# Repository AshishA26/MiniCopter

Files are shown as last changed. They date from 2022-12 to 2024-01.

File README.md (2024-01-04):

# MiniCopter
A mini quadcopter that is lightweight (~100g) and designed for agility. It is made using an Arduino Nano, an MPU6050 for orientation sensing, an NRF24L01 for wireless communication, MOSFETs that act as motor drivers, and 8520 motors. The quadcopter is controlled using a custom transmitter that has 2 joysticks and an NRF24L01, and uses PID motor control for stabilizing roll and pitch of the quadcopter. In addition, I created a custom PCB to house all these components and allow for better wiring, testing, and weight reduction.

Programmed in `Arduino IDE`, models created in `Autodesk Inventor`, schematics and PCB created in `KiCad`.

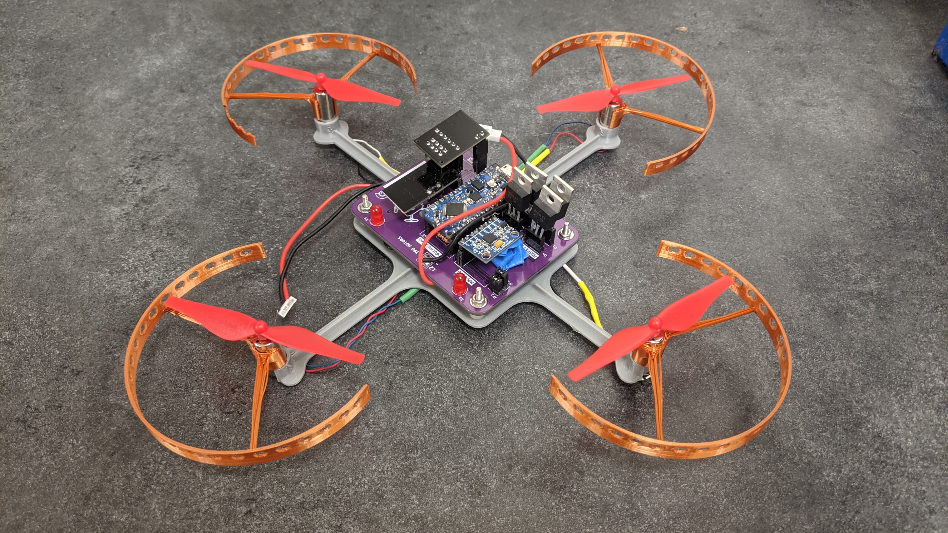
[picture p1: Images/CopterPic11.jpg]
CopterPic11

CopterGif1

Demo showing the PID motor control of the quadcopter that allows for the quadcopter to stabilize and balance ([full video](https://www.youtube.com/watch?v=k4_8MwJ_Zw4)):
CopterGif2

## PCB Design
My original design used a perfboard, but I eventually designed a 2-layer PCB that would not only simplify debugging and wire routing, but also allow for some weight reduction. 

The PCB contains all circuitry and the connections between them. The placement, orientation, and connections of each component was carefully considered when making decisions on the design of the PCB. The size of the PCB itself was also an important factor for me to consider because I needed to be the smallest and most optimal size it could be in order to reduce the weight on the quadcopter.

The PCB also acts as custom motor drivers for each motor by employing the use of MOSFETs, as normal Arduino motor drivers available online are too large and are not meant for high current flow and high speeds. 

Through calculations, I determined the trace size required for each component on the board, such as the LiPo battery connections needing thicker traces due to the high current. After various tests, it was found that dupont connectors could not be used to transfer current to the motors as the end connectors had resistance, so having a PCB with custom trace sizes was very useful.

Additionally, through testing on the Perfboard, I found that 2 LiPo batteries were required as I not only needed to power the 4 motors, but also the Arduino (which also powers other components).

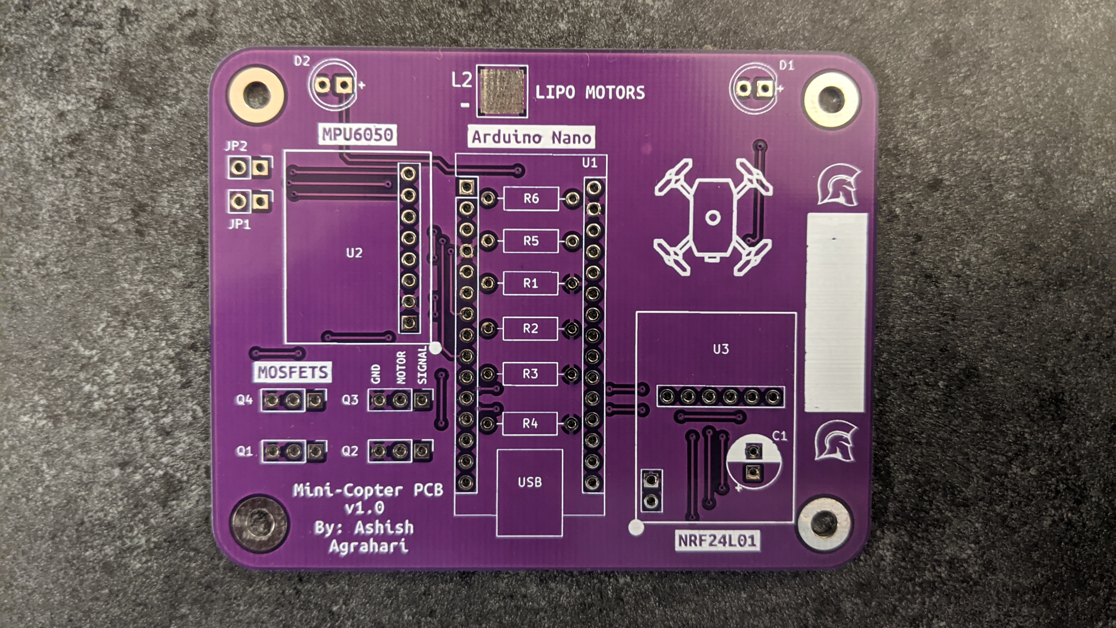
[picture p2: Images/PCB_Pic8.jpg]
PCB_Pic8

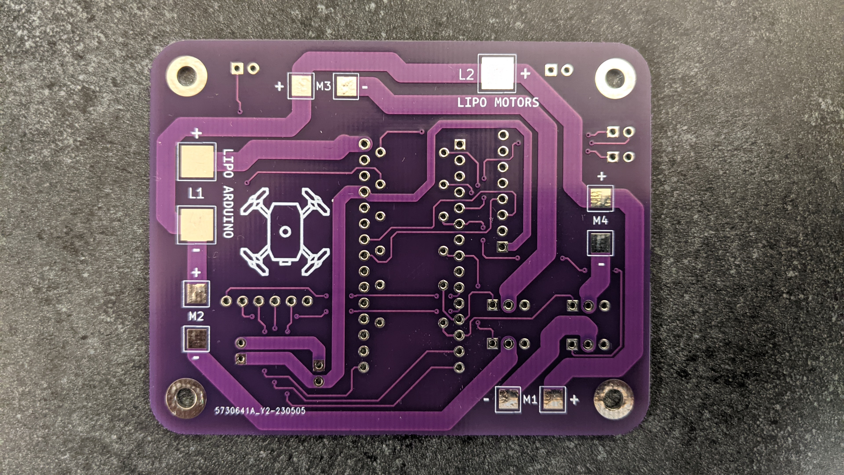
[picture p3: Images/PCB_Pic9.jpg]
PCB_Pic9

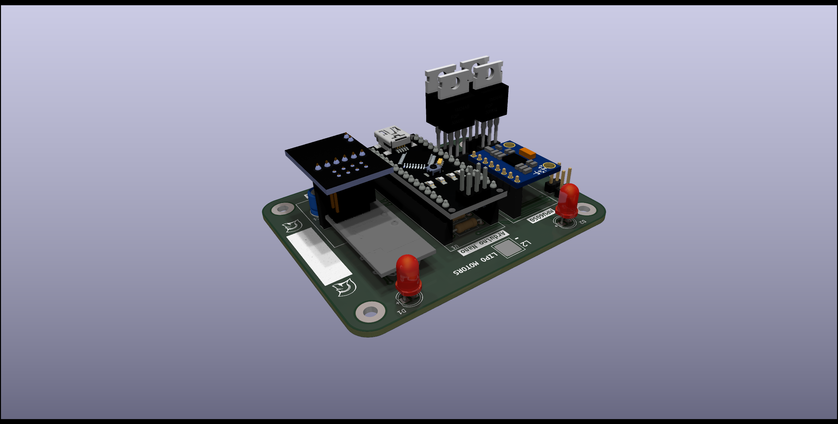
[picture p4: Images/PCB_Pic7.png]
PCB_Pic7


### Routing
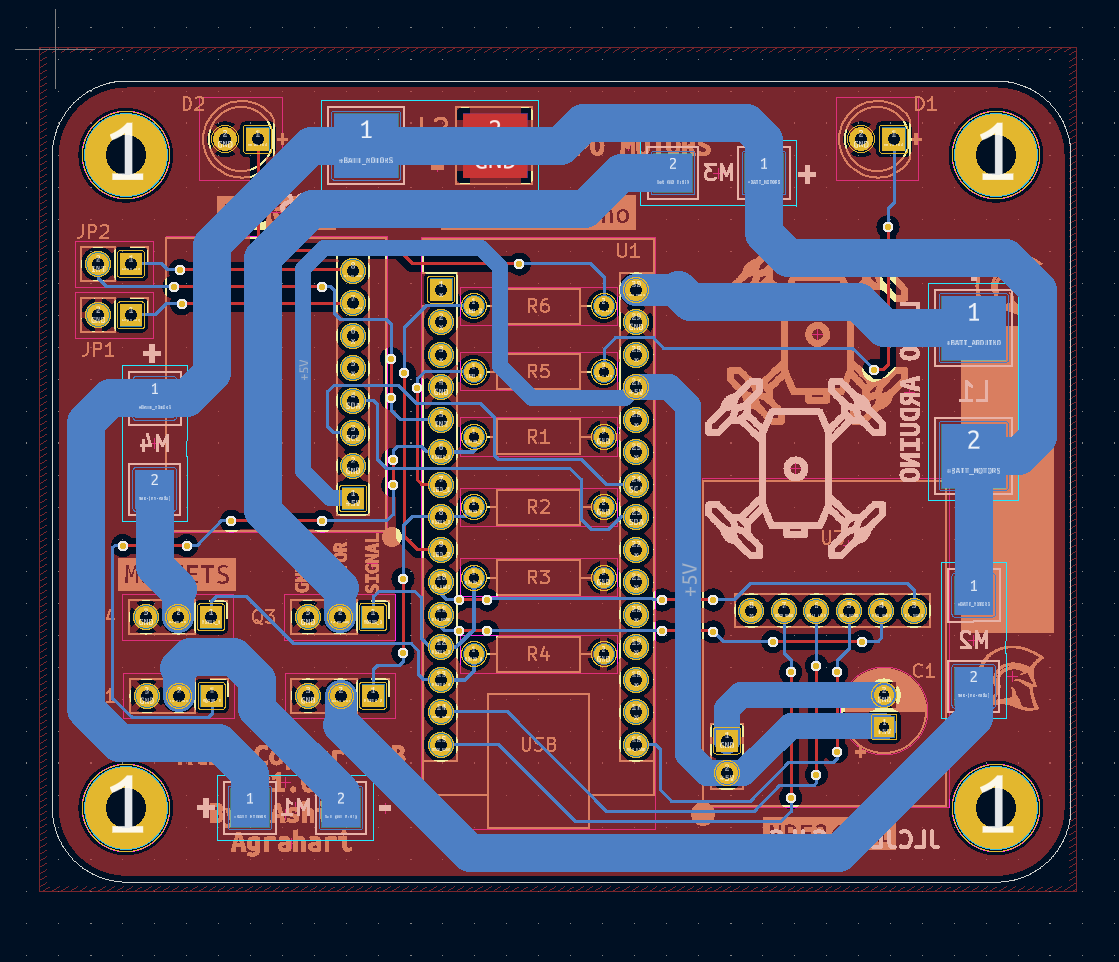
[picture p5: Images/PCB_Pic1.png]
PCB_Pic1

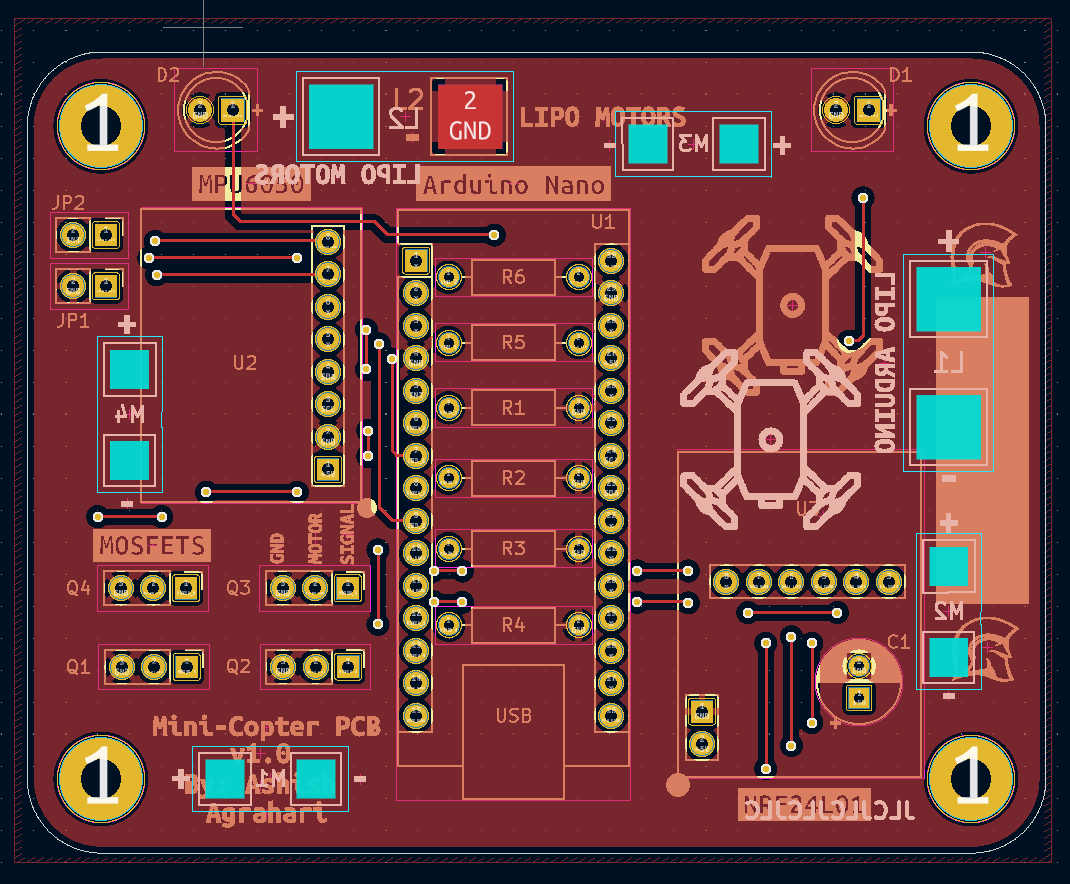
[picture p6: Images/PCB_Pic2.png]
PCB_Pic2

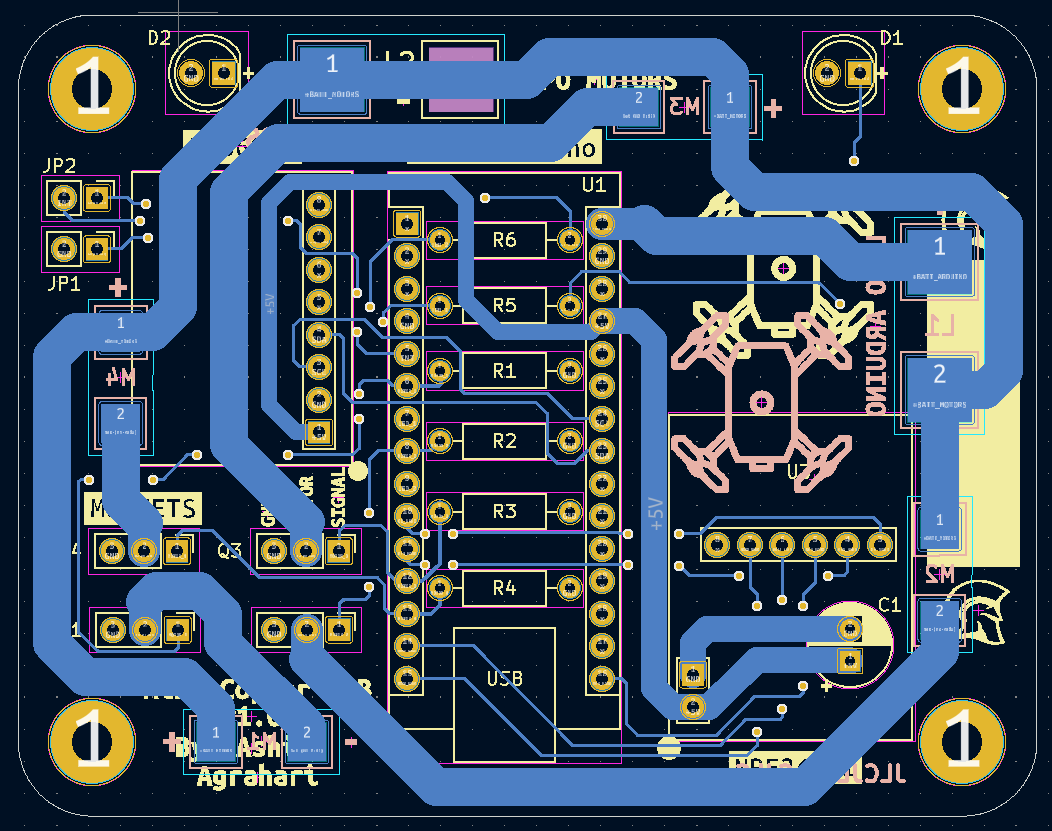
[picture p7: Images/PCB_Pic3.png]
PCB_Pic3


### Original Perfboard Design

| Perfboard Front Side | Perfboard Back Side |
| :---: | :---: |
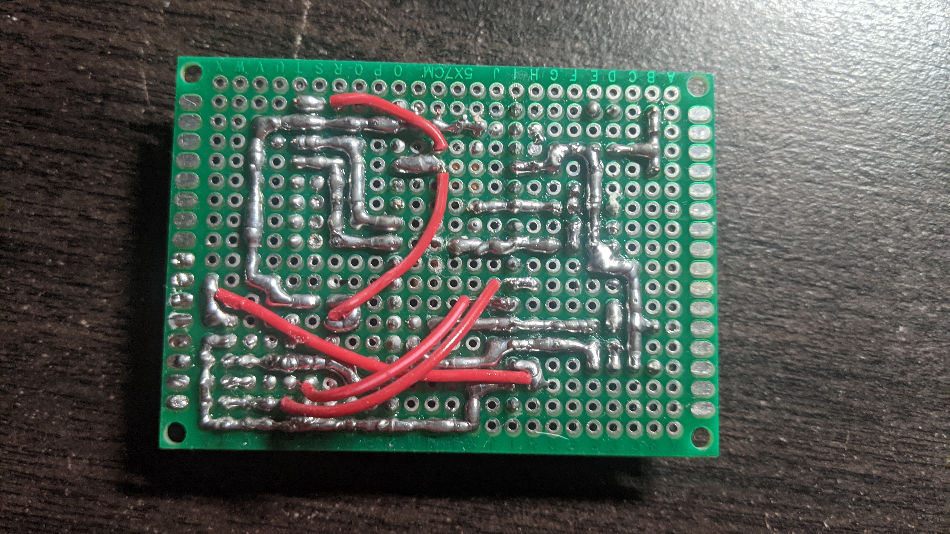
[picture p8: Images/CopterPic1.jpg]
CopterPic1
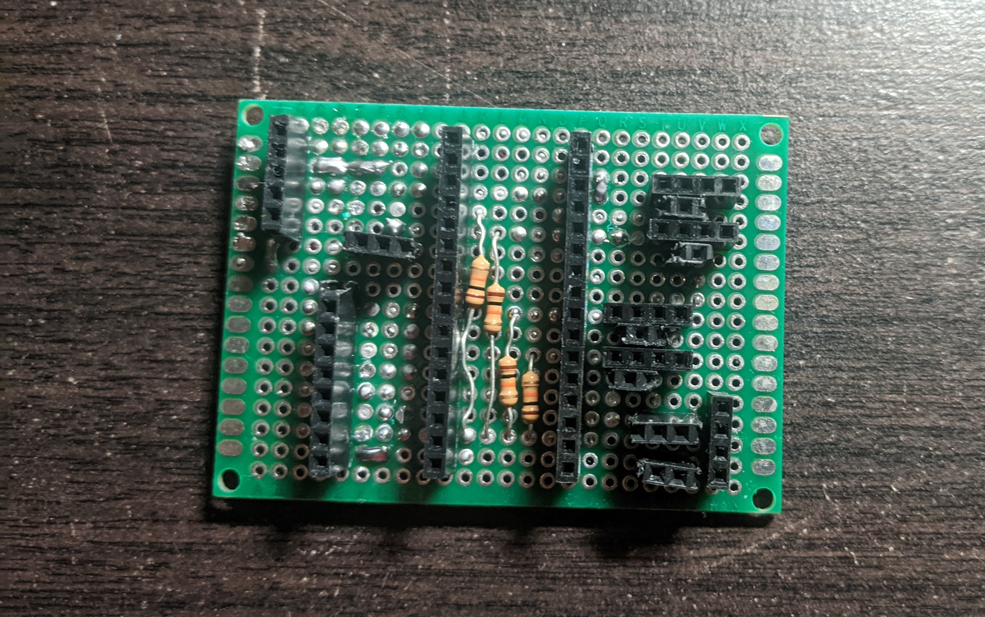
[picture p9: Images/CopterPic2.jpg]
CopterPic2
|   |  |
| Back side of complete perfboard | Perfboard on minicoptoper |
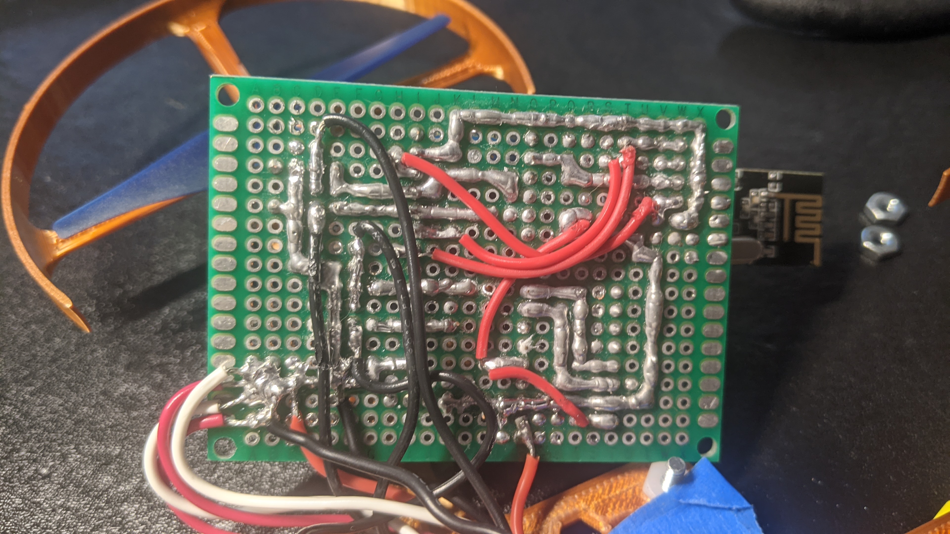
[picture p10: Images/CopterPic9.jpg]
CopterPic9
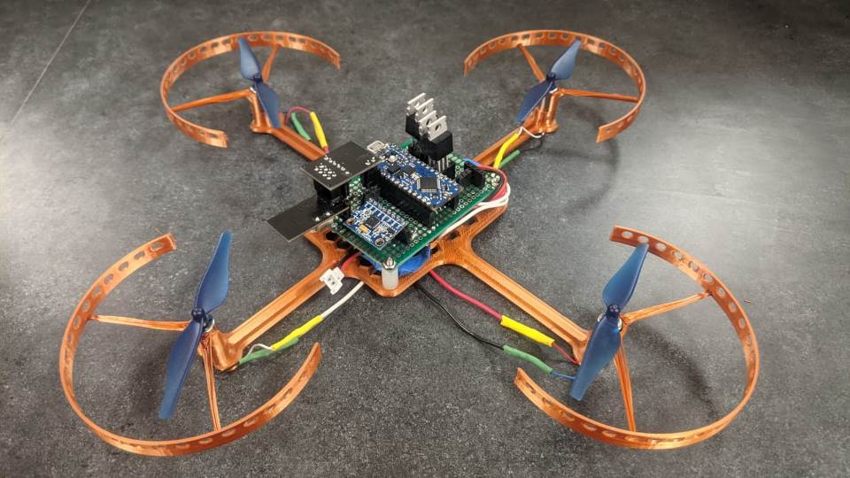
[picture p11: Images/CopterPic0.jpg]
CopterPic0
|   |  |

## Schematics
CopterSchematic
CopterSchematic

## Part Pictures
After many tests and designs, the final chassis has been built such that the frame is strong and firm enough, while greatly reducing weight. The propellor gaurds have also been iteratively designed after numerous tests such that it protects people and the quadcopter, while also being very lightweight.

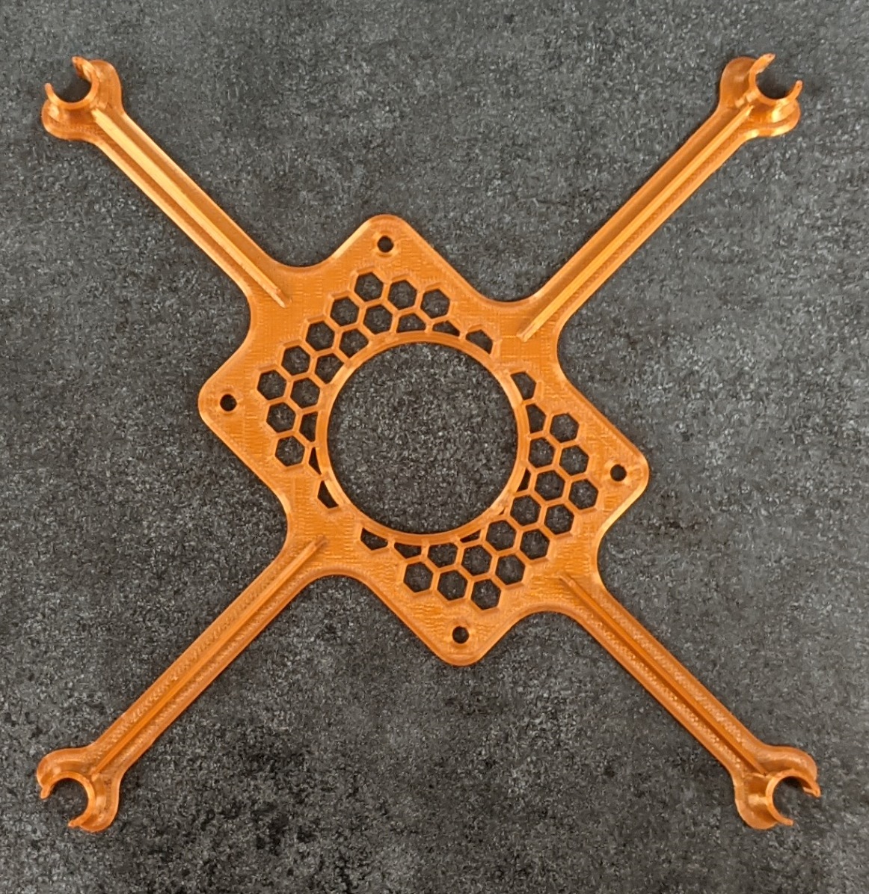
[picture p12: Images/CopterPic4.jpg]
CopterPic4

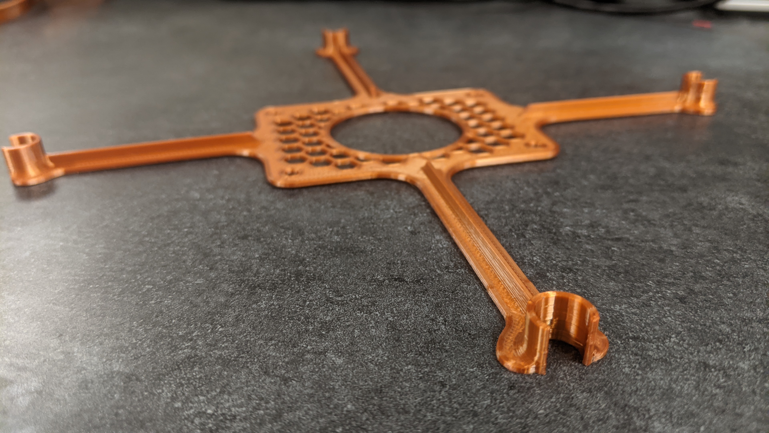
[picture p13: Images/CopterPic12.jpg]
CopterPic12

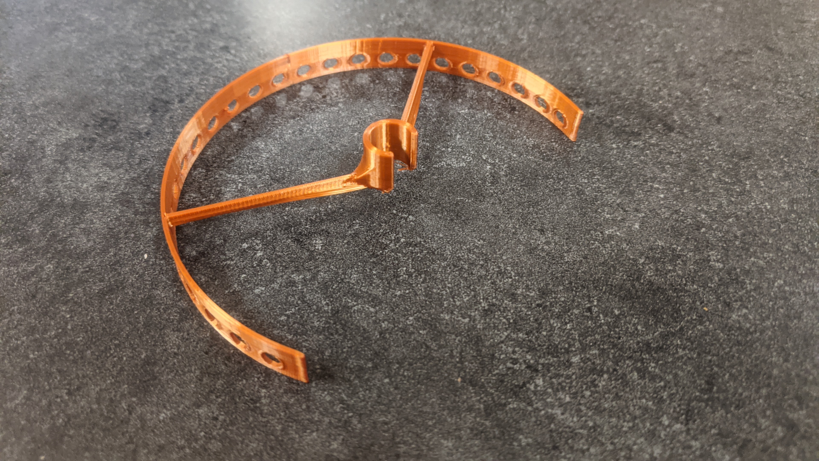
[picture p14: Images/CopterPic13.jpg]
CopterPic13


## Other Tests

Checkout some [flight testing](https://www.youtube.com/watch?v=XLUD_ImCz4A).

Checkout a demo of [the joystick wirelessly controlling a motor](https://www.youtube.com/watch?v=rh6yMr4QYGM).

To determine the strength of each motor, I 3D printed some parts and flipped the motor upside down to conduct a thrust analysis. This allowed me to see if the MOSFETs and batteries would be able to supply enough current to the motors.

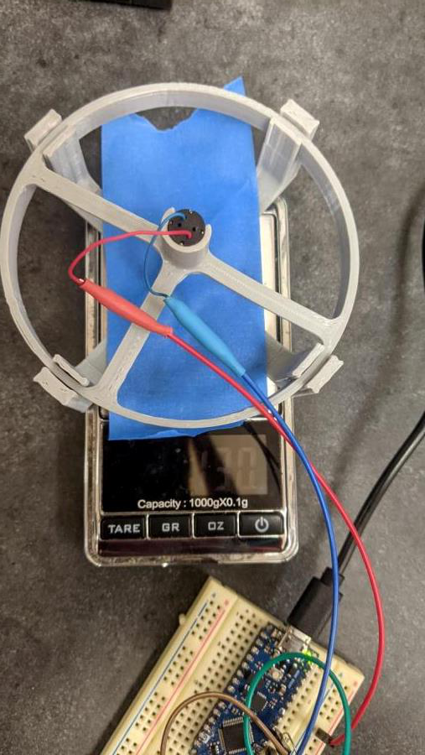
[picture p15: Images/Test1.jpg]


## Setup
- To open the schematics and pcb, install my [KiCAD libraries](https://github.com/AbhinavA10/kicad-libraries).

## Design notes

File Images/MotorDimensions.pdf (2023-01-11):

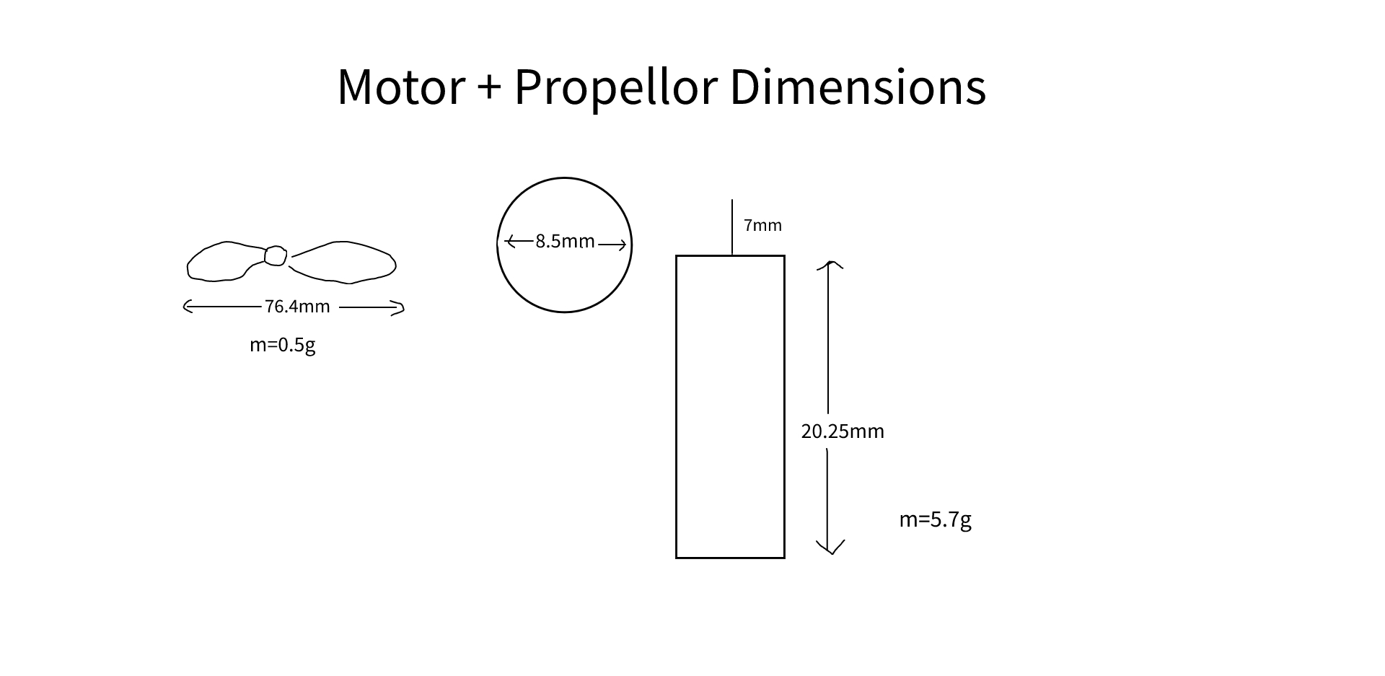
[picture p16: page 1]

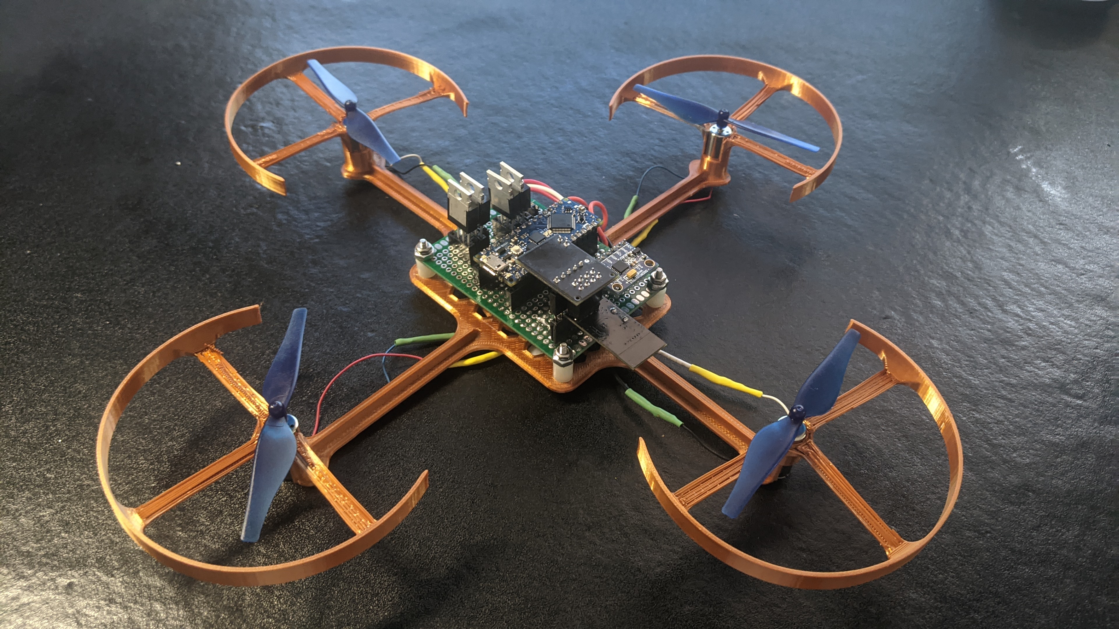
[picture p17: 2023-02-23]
Images/CopterPic10.jpg

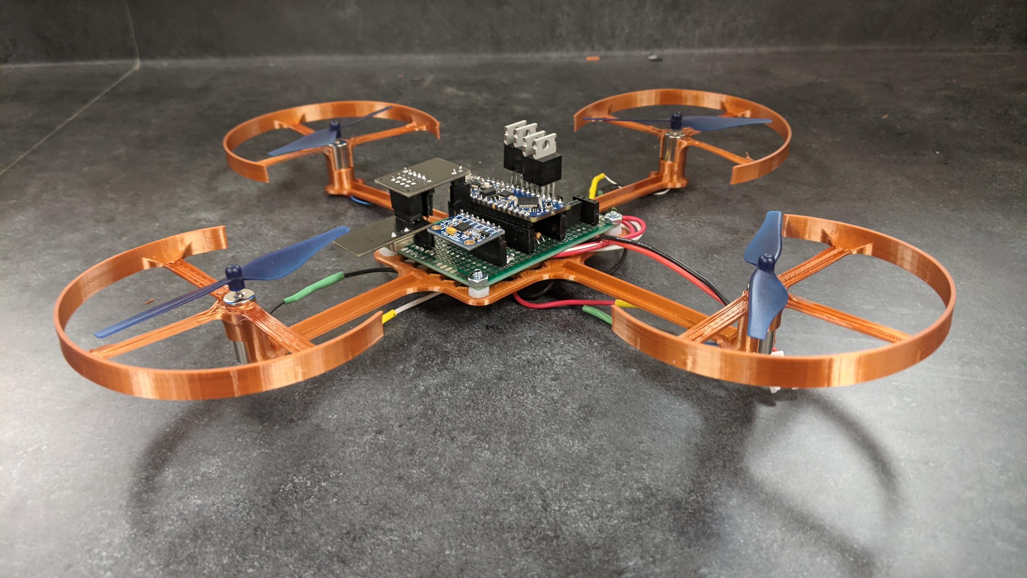
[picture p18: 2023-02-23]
Images/CopterPic7.jpg

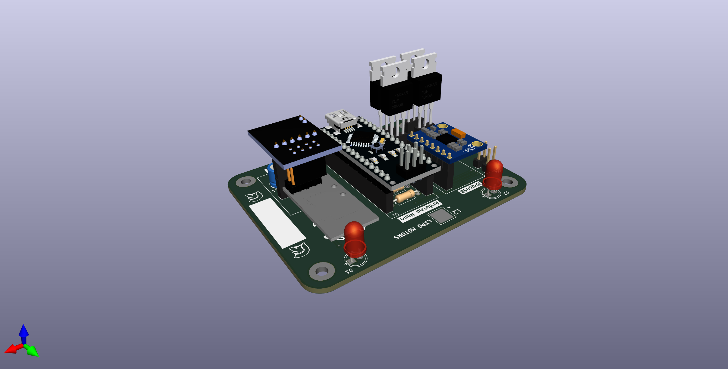
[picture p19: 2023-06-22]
Images/PCB_Pic6.png

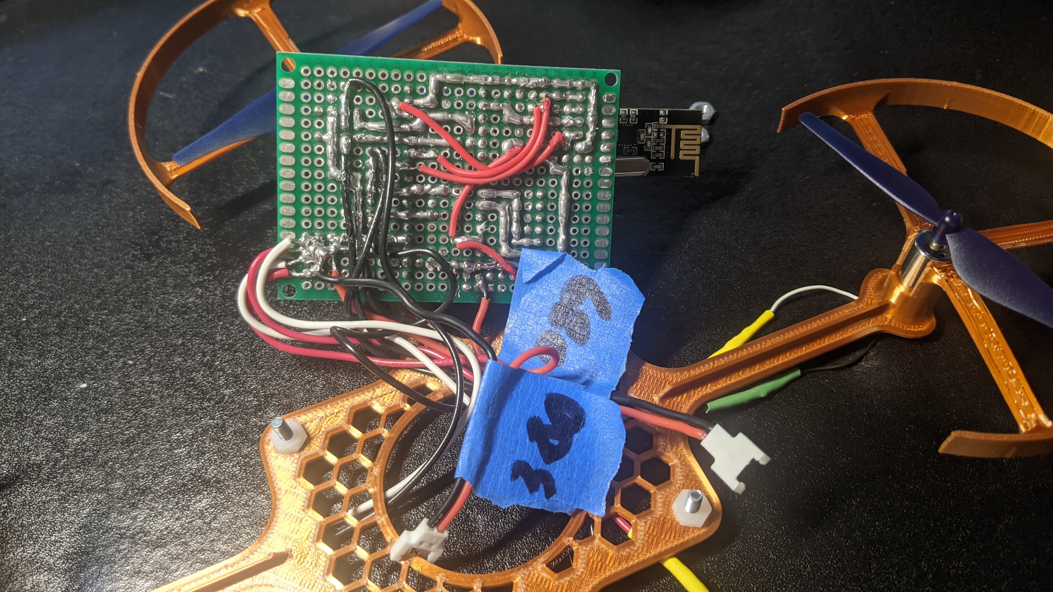
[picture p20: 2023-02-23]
Images/CopterPic8.jpg

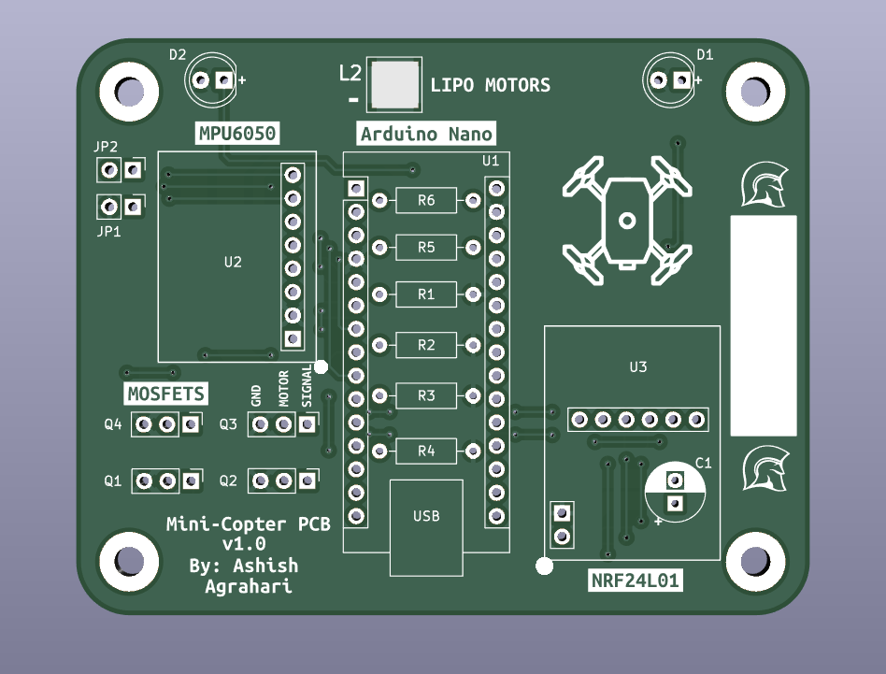
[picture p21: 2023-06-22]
Images/PCB_Pic4.png

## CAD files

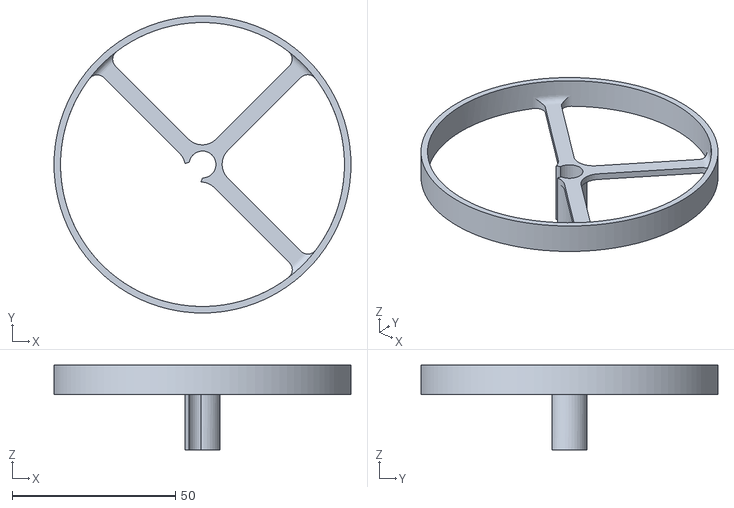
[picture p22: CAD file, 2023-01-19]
Models/ForTesting/GuardV1.stl
91.0 x 91.0 x 26.0

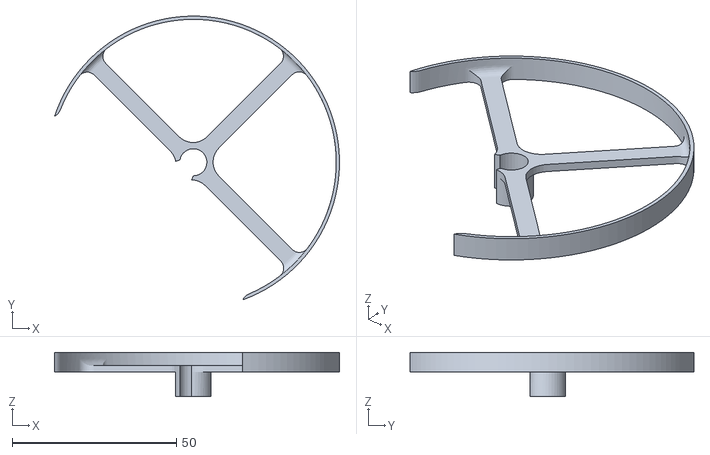
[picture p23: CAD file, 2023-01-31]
Models/PropellorGuardV2_Ashish.stl
86.8 x 86.4 x 13.5

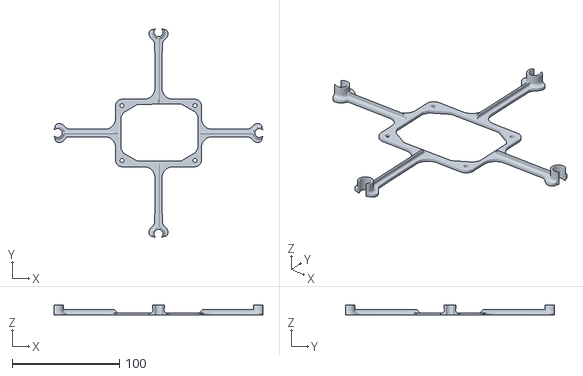
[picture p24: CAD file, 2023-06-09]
Models/STL/MiniCopterChassisLighterV3.stl
194.8 x 194.8 x 9.50

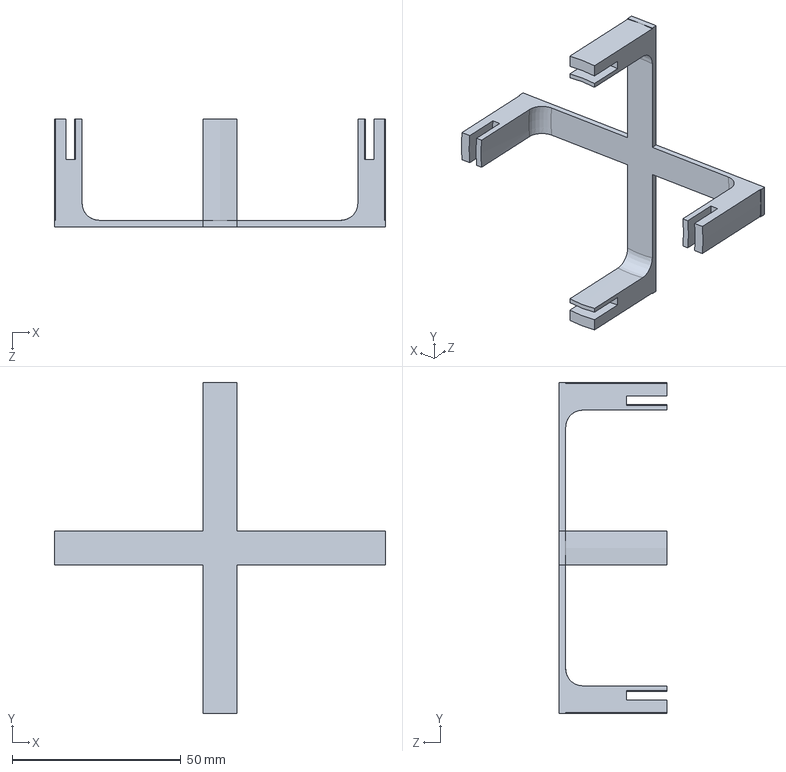
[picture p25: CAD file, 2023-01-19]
Models/ForTesting/GuardStand.SLDPRT
98.0 x 98.0 x 32.0 mm

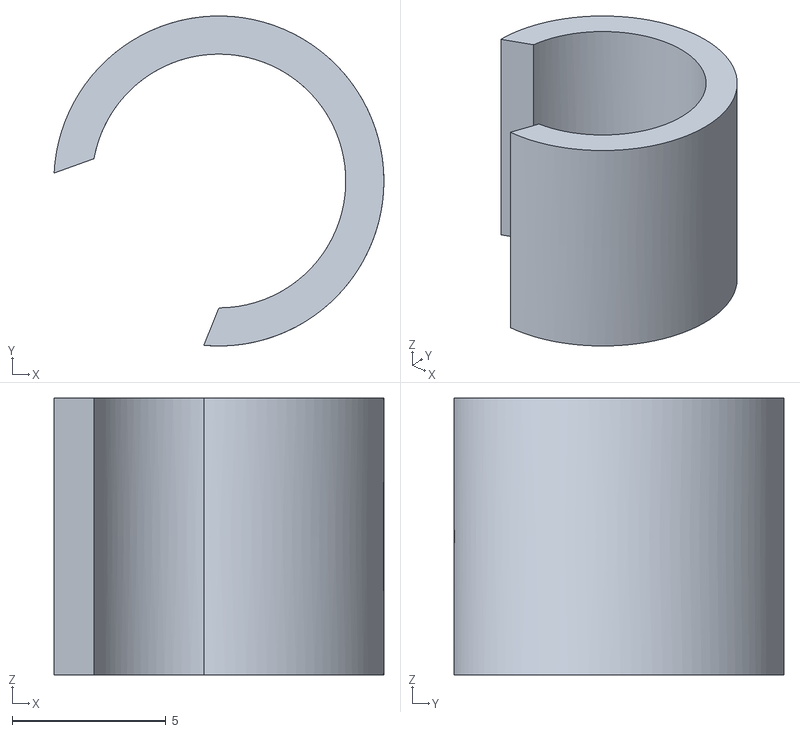
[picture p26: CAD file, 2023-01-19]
Models/GuardTest.stl
10.7 x 10.7 x 9.00

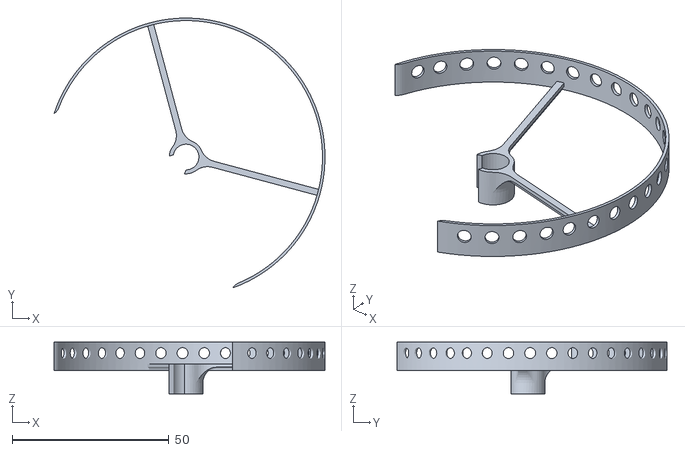
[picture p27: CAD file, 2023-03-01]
Models/STL/PropellorGuardLighter.stl
86.4 x 86.0 x 16.5

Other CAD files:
Models/Assembly/ChassisLeg.ipt
Models/Assembly/MiniCopterAssembly.iam
Models/Assembly/MiniCopterChassisLighterV3.ipt
Models/Assembly/PropellorGuard.ipt
Models/Assembly/PropellorGuardLighter.ipt
Models/ChassisLegV1.ipt
Models/ForTesting/GuardStand.STL
Models/ForTesting/GuardV1.ipt
Models/GuardTest.ipt
Models/MiniCopterChassisV1.ipt
Models/MotorDemoV1.ipt
Models/PropellorGuardV2_Ashish.ipt

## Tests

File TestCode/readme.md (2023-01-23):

## Libraries needed:
Arduino:
- I2C dev
- MPU6050
- RF24

Processing:
- toxiclibs_p5
- toxiclibscore

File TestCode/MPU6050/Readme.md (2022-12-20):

# MPU6050 test
## Pins:
- `MPU` --> `Arduino Nano`
- `VCC` --> `Vin`
- `GND` --> `GND`
- `SCL` --> `A5`
- `SDA` --> `A4`
- `INT` --> `D2`

## Instructions:
- In the `MPUTeapot.pde`, you will have to change line 74 to have your COM port (`String portName = "COM12";`) 
- In the `MPU6050_DMP6.ino`, you will have to uncomment `#define OUTPUT_TEAPOT` if you want it to work with the teapot demo, or `#define OUTPUT_READABLE_YAWPITCHROLL` if you want to read the output

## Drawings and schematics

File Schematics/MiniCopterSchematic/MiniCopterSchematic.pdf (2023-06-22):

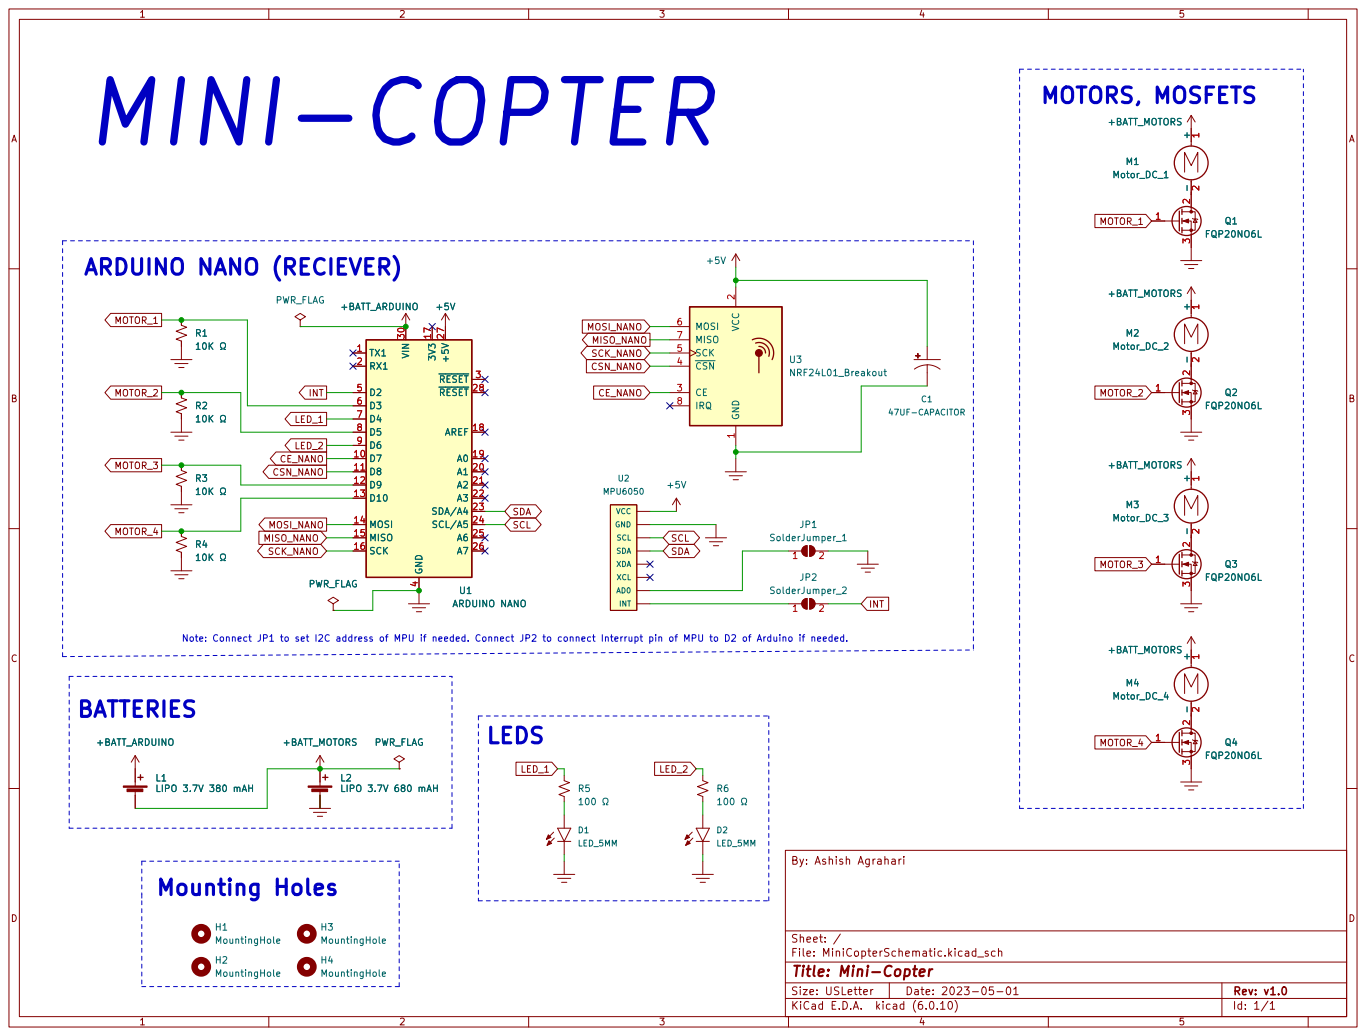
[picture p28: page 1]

MOTORS, MOSFETS MINI-COPTER

2 CE 3 ~{CSN} 4 SCK 5 MOSI 6 MISO 7

File: MiniCopterSchematic.kicad_sch Sheet: / By: Ashish Agrahari

Id: 1/1 Title: Mini-Copter

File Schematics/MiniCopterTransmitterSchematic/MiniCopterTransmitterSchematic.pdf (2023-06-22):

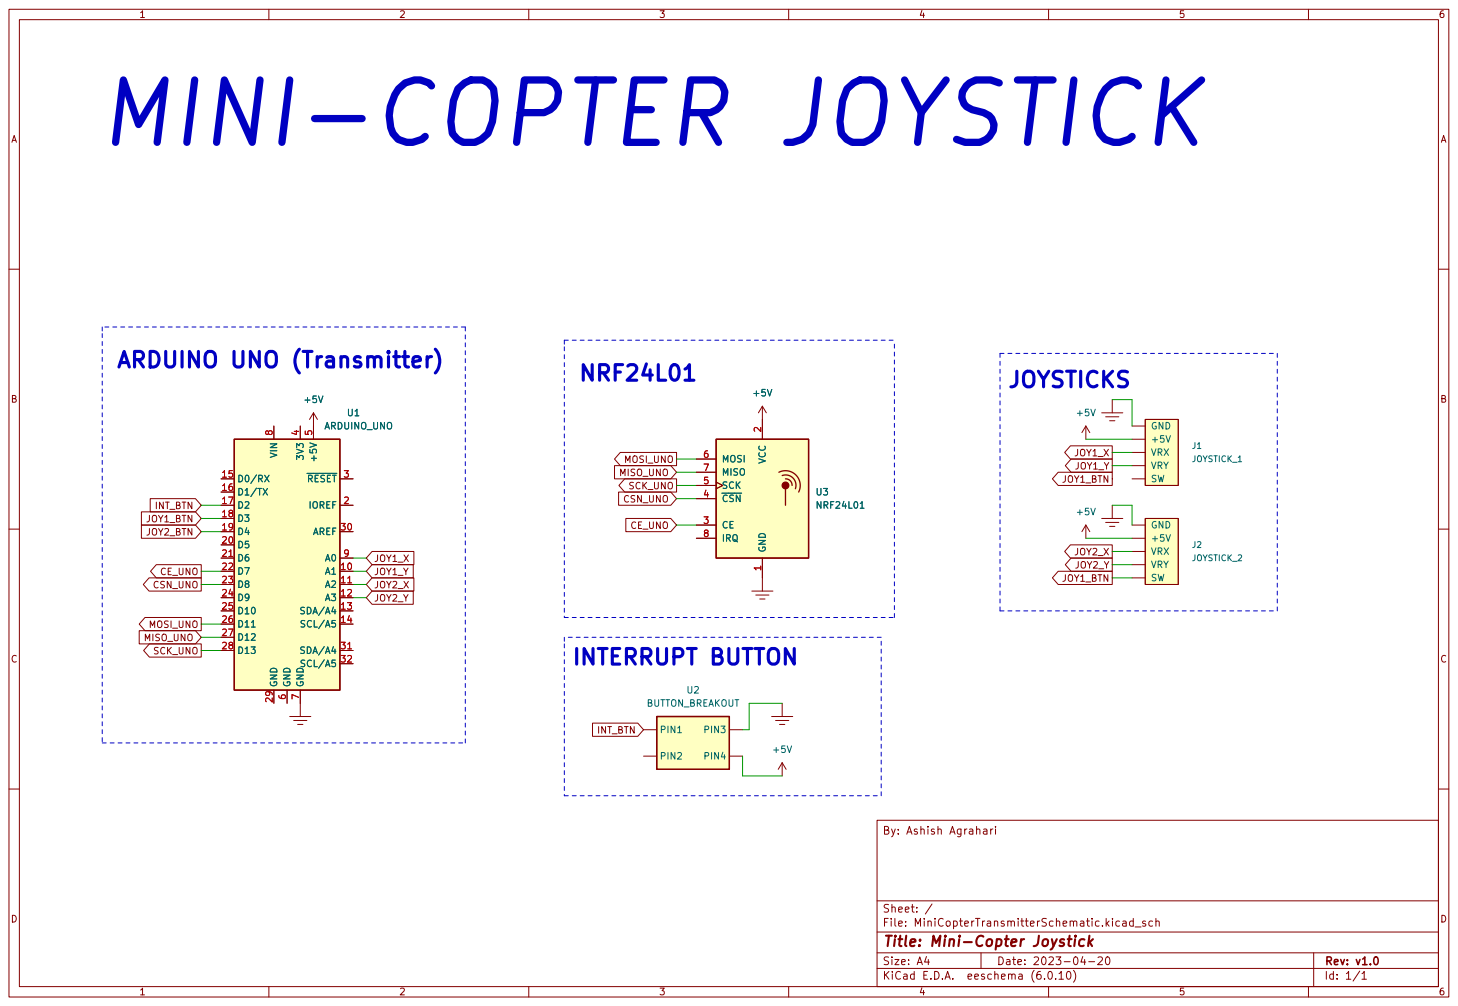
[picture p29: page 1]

2 CE 3 ~{CSN} 4 SCK 5 MOSI 6 MISO 7

Id: 1/1 Title: Mini-Copter Joystick

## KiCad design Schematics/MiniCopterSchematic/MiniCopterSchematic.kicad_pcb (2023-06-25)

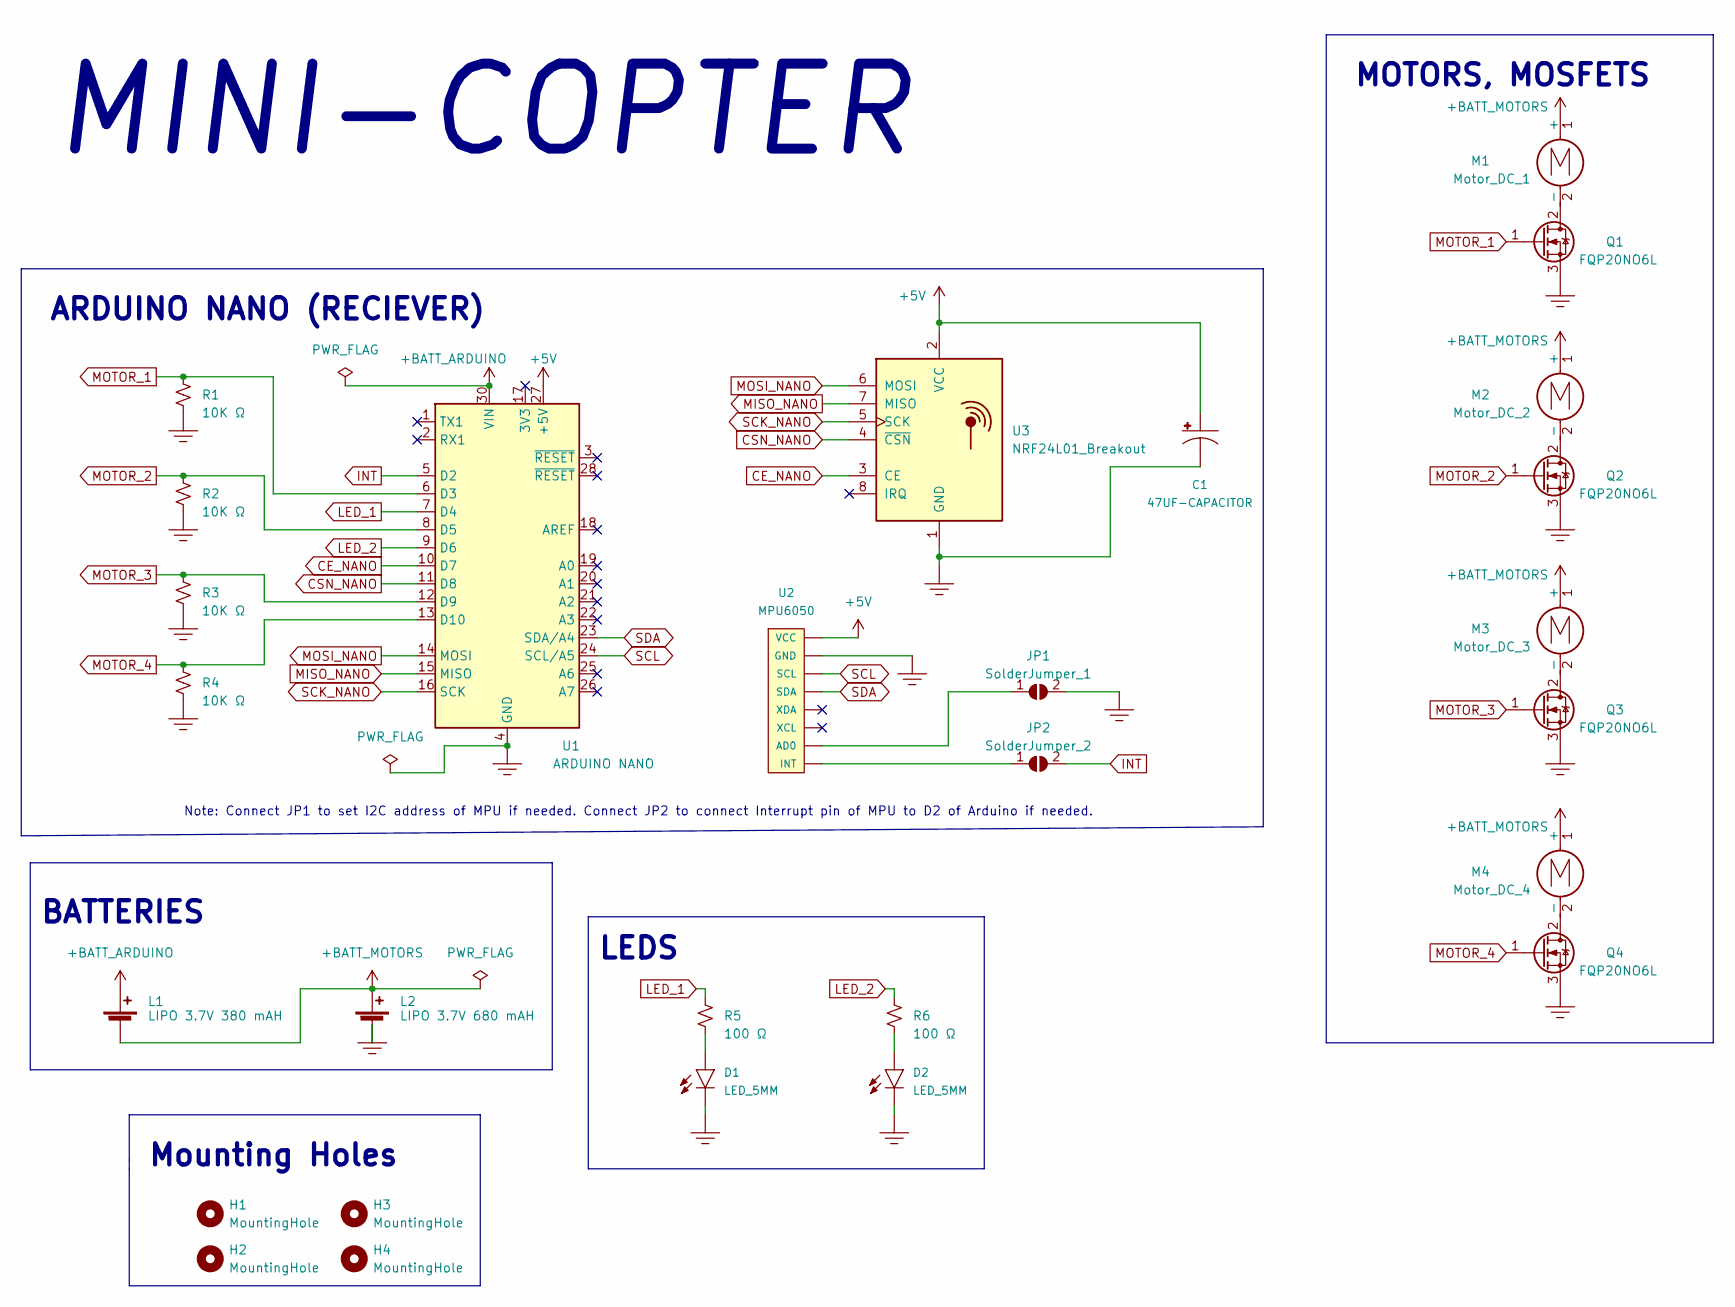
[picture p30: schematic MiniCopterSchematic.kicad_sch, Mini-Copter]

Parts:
C1: 47UF-CAPACITOR; CP_Radial_D6.3mm_P2.50mm
D1, D2: LED_5MM; LED_D5.0mm
H1, H2, H3, H4: MountingHole; MountingHole_3.2mm_M3_Pad
JP1: SolderJumper_1; PinHeader_1x02_P2.54mm_Vertical
JP2: SolderJumper_2; PinHeader_1x02_P2.54mm_Vertical
L1: LIPO 3.7V 380 mAH; PowerPad_Pair_5.0x5.0mm
L2: LIPO 3.7V 680 mAH; PowerPad_Pair_5.0x5.0mm_1PadFlipped
M1: Motor_DC_1; PowerPad_Pair_3.0x3.0mm
M2: Motor_DC_2; PowerPad_Pair_3.0x3.0mm
M3: Motor_DC_3; PowerPad_Pair_3.0x3.0mm
M4: Motor_DC_4; PowerPad_Pair_3.0x3.0mm
Q1, Q2, Q3, Q4: FQP20NO6L; 3Pin_MOSFET_MotorDriver
R1, R2, R3, R4: 10K Ω; R_Axial_DIN0207_L6.3mm_D2.5mm_P10.16mm_Horizontal
R5, R6: 100 Ω; R_Axial_DIN0207_L6.3mm_D2.5mm_P10.16mm_Horizontal
U1: ARDUINO NANO; Arduino_Nano
U2: MPU6050
U3: NRF24L01_Breakout

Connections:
+5V: C1.1 (+), U1.27 (+5V), U2.1 (VCC), U3.2 (VCC)
+BATT_ARDUINO: L1.1 (+), U1.30 (VIN)
+BATT_MOTORS: L1.2 (-), L2.1 (+), M1.1 (+), M2.1 (+), M3.1 (+), M4.1 (+)
CE_NANO: U1.10 (D7), U3.3 (CE)
CSN_NANO: U1.11 (D8), U3.4 (~CSN)
GND: C1.2 (-), D1.2, D2.2, JP1.2 (B), L2.2 (-), Q1.3 (S), Q2.3 (S), Q3.3 (S), Q4.3 (S), R1.2, R2.2, R3.2, R4.2, U1.4 (GND), U1.29 (GND), U2.2 (GND), U3.1 (GND)
INT: JP2.2 (B), U1.5 (D2)
LED_1: R5.1, U1.7 (D4)
LED_2: R6.1, U1.9 (D6)
MISO_NANO: U1.15 (MISO), U3.7 (MISO)
MOSI_NANO: U1.14 (MOSI), U3.6 (MOSI)
MOTOR_1: Q1.1 (G), R1.1, U1.6 (D3)
MOTOR_2: Q2.1 (G), R2.1, U1.8 (D5)
MOTOR_3: Q3.1 (G), R3.1, U1.12 (D9)
MOTOR_4: Q4.1 (G), R4.1, U1.13 (D10)
unnamed: D1.1, R5.2
unnamed: D2.1, R6.2
unnamed: JP1.1 (A), U2.7 (AD0)
unnamed: JP2.1 (A), U2.8 (INT)
unnamed: M1.2 (-), Q1.2 (D)
unnamed: M2.2 (-), Q2.2 (D)
unnamed: M3.2 (-), Q3.2 (D)
unnamed: M4.2 (-), Q4.2 (D)
SCK_NANO: U1.16 (SCK), U3.5 (SCK)
SCL: U1.24 (SCL/A5), U2.3 (SCL)
SDA: U1.23 (SDA/A4), U2.4 (SDA)

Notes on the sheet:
ARDUINO NANO (RECIEVER)
Note: Connect JP1 to set I2C address of MPU if needed. Connect JP2 to connect Interrupt pin of MPU to D2 of Arduino if needed.
MINI-COPTER
BATTERIES
LEDS
Mounting Holes
MOTORS, MOSFETS

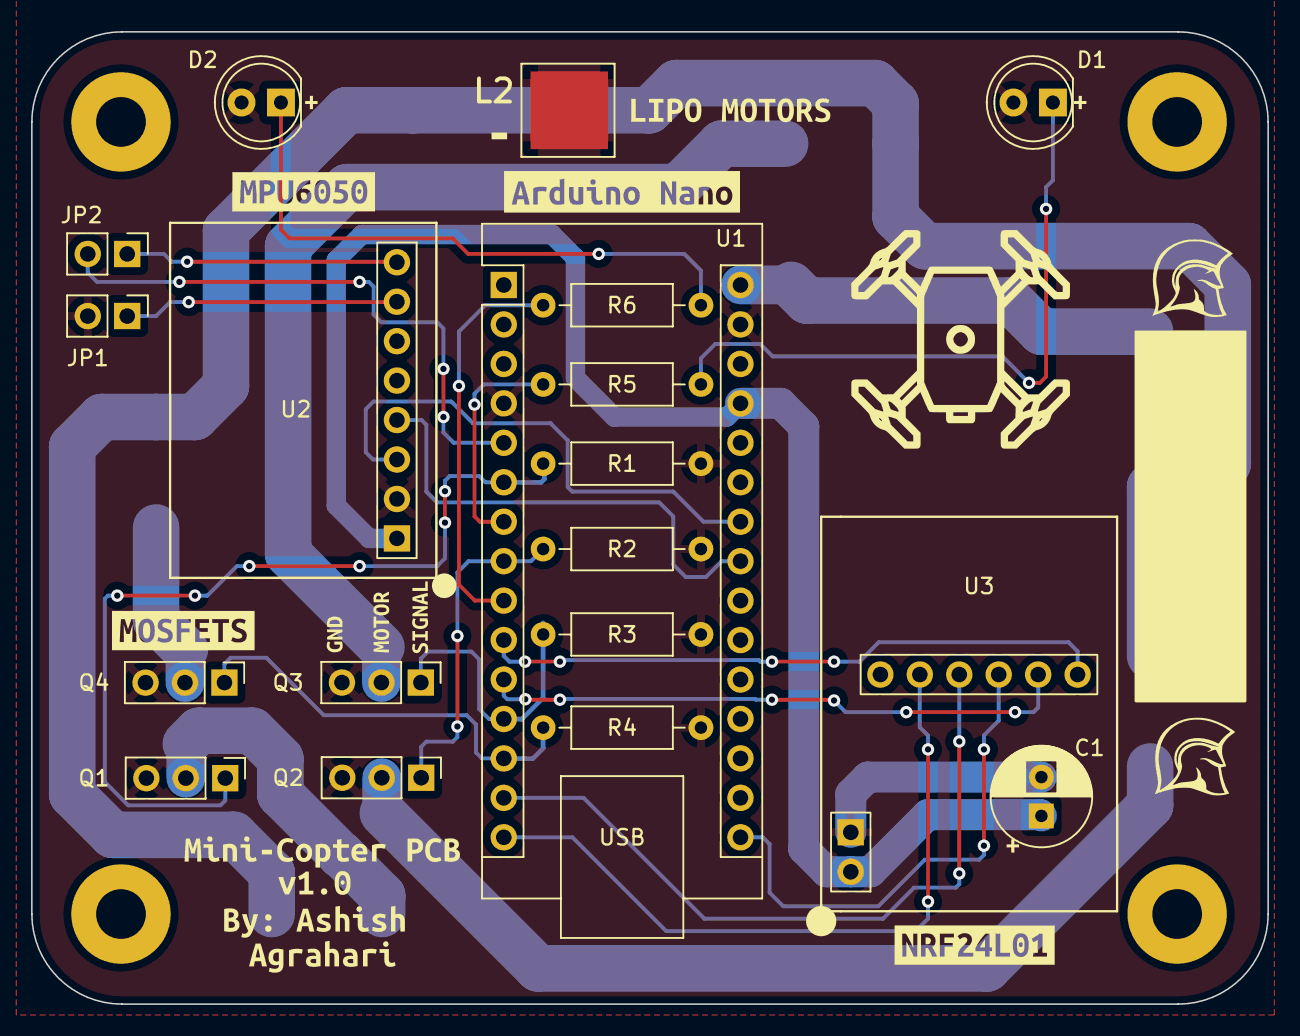
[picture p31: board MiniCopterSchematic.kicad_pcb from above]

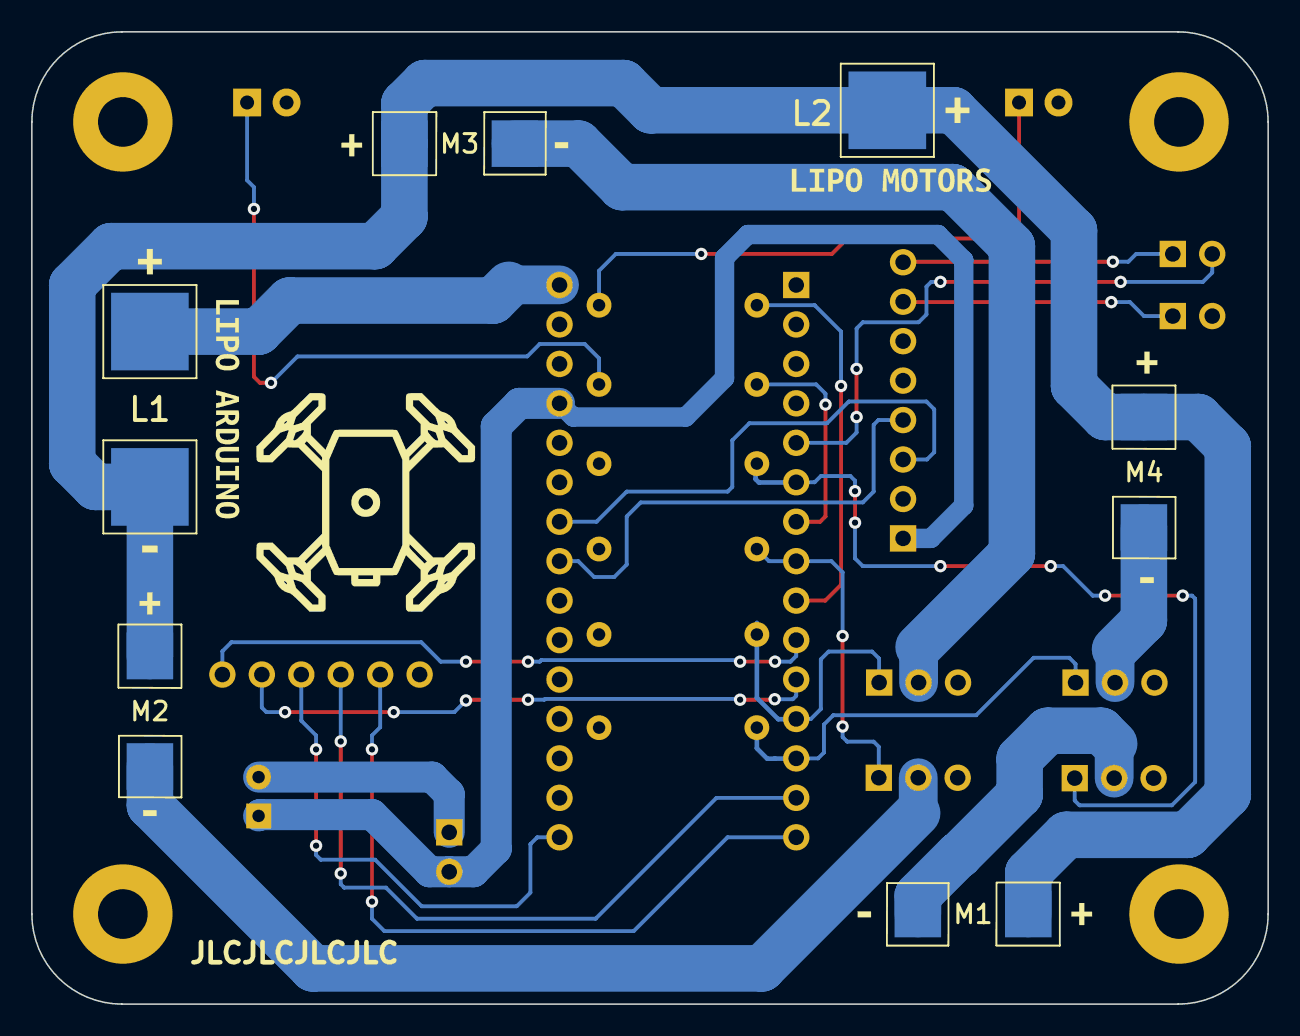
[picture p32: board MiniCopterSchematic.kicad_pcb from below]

Board: 2 copper layers, 79.6 x 62.6 mm, 57 parts (9 on the bottom side), 26 nets.

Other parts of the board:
kibuzzard-644F1CFC: G***; kibuzzard-644F1CFC
kibuzzard-644F1D01: G***; kibuzzard-644F1D01
kibuzzard-644F1F4C: G***; kibuzzard-644F1F4C
kibuzzard-644F1F5E: G***; kibuzzard-644F1F5E
kibuzzard-644F1F53: G***; kibuzzard-644F1F53
kibuzzard-644F1F59: G***; kibuzzard-644F1F59
kibuzzard-644F15D5: G***; kibuzzard-644F15D5
kibuzzard-644F152E: G***; kibuzzard-644F152E
kibuzzard-644F167C: G***; kibuzzard-644F167C
kibuzzard-644F1527: G***; kibuzzard-644F1527
kibuzzard-644F2052: G***; kibuzzard-644F2052
kibuzzard-644F2068: G***; kibuzzard-644F2068
kibuzzard-644F2071: G***; kibuzzard-644F2071
kibuzzard-6440B80B, kibuzzard-6440B80B#2, kibuzzard-6440B80B#3, kibuzzard-6440B80B#4: G***; kibuzzard-6440B80B
kibuzzard-6440B803, kibuzzard-6440B803#2, kibuzzard-6440B803#3, kibuzzard-6440B803#4: G***; kibuzzard-6440B803
kibuzzard-6440D5EF: G***; kibuzzard-6440D5EF
kibuzzard-6440D61E: G***; kibuzzard-6440D61E
kibuzzard-6440D635: G***; kibuzzard-6440D635
kibuzzard-6452D829: G***; kibuzzard-6452D829
kibuzzard-6452DC3B: G***; kibuzzard-6452DC3B
kibuzzard-6452DC31: G***; kibuzzard-6452DC31
kibuzzard-6452DC36: G***; kibuzzard-6452DC36
kibuzzard-6452DC40: G***; kibuzzard-6452DC40

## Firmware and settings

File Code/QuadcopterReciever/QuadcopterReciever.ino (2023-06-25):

// By Ashish Agrahari
// Code for circuitboard that is placed on the quadcopter (Arduino Nano) and is the "reciever"

// Include libraries
#include "I2Cdev.h"
#include "MPU6050_6Axis_MotionApps20.h"
#include <SPI.h>
#include <nRF24L01.h>
#include <RF24.h>
#include <Wire.h>

// Defining motor pins
#define Motor1Pin 3
#define Motor2Pin 5
#define Motor3Pin 9
#define Motor4Pin 10

// ************ Initialize nRF24L01 variables *****************
RF24 radio(7, 8);   // nRF24L01 (CE, CSN)
const byte address[6] = "00010"; // Wireless communication address
unsigned long lastReceiveTime = 0;
unsigned long currentTime = 0;

// Max size of this struct is 32 bytes - NRF24L01 buffer limit
// Creating package to recieve data in:
struct Data_Package {
  byte j1PotX;
  byte j1PotY;
  byte j1Button;
  byte j2PotX;
  byte j2PotY;
  byte j2Button;
};
Data_Package data; //Create a variable with the above structure

// ************ Initialize MPU6050 variables *****************
MPU6050 mpu;

#define INTERRUPT_PIN 2  // specific interrupt pin on Arduino nano every

// MPU control/status variables
bool dmpReady = false;  // set true if DMP init was successful
uint8_t mpuIntStatus;   // holds actual interrupt status byte from MPU
uint8_t devStatus;      // return status after each device operation (0 = success, !0 = error)
uint16_t packetSize;    // expected DMP packet size (default is 42 bytes)
uint16_t fifoCount;     // count of all bytes currently in FIFO
uint8_t fifoBuffer[64]; // FIFO storage buffer

// MUP Orientation/motion variables
Quaternion q;           // [w, x, y, z]         quaternion container
VectorInt16 aa;         // [x, y, z]            accel sensor measurements
VectorInt16 aaReal;     // [x, y, z]            gravity-free accel sensor measurements
VectorInt16 aaWorld;    // [x, y, z]            world-frame accel sensor measurements
VectorFloat gravity;    // [x, y, z]            gravity vector
float euler[3];         // [psi, theta, phi]    Euler angle container
float ypr[3];           // [yaw, pitch, roll]   yaw/pitch/roll container and gravity vector

volatile bool mpuInterrupt = false;     // indicates whether MPU interrupt pin has gone high
void dmpDataReady() {
  mpuInterrupt = true;
}

// Create variables for PID control of motors
int target_angle = 0;
int kp = 20;
float error_R = 0;
float angleChange_R = 0;
float speedChange_R = 0;
float error_P = 0;
float angleChange_P = 0;
float speedChange_P = 0;

int motorSpeed1 = 0;
int motorSpeed2 = 0;
int motorSpeed3 = 0;
int motorSpeed4 = 0;

void setup() {
  Serial.begin(9600); // Open serial port
  // Note: Baud rate at 115200 will make Serial fasterr but they will print out MPU slower than the joystick

  // Begin radio communication using nRF24L01
  radio.begin();
  radio.openReadingPipe(0, address);
  radio.setAutoAck(false);
  radio.setDataRate(RF24_250KBPS);
  radio.setPALevel(RF24_PA_MIN);
  radio.startListening(); //  Set the module as receiver
  resetData(); // Initally reset all joystick input values

  // ************ MPU6050 setup *****************

  // join I2C bus (I2Cdev library doesn't do this automatically)
#if I2CDEV_IMPLEMENTATION == I2CDEV_ARDUINO_WIRE
  Wire.begin();
  Wire.setClock(400000); // 400kHz I2C clock. Comment this line if having compilation difficulties
  //Wire.setWireTimeout(3000, true); // VERY IMPORTANT!!! THIS FIXES THE I2C BUS FROM HANGING
#elif I2CDEV_IMPLEMENTATION == I2CDEV_BUILTIN_FASTWIRE
  Fastwire::setup(400, true);
#endif

  while (!Serial); // wait for Leonardo enumeration, others continue immediately

  // initialize device
  Serial.println(F("Initializing I2C devices..."));
  mpu.initialize();
  pinMode(INTERRUPT_PIN, INPUT);

  // verify connection
  Serial.println(F("Testing device connections..."));
  Serial.println(mpu.testConnection() ? F("MPU6050 connection successful") : F("MPU6050 connection failed"));

  // load and configure the DMP (Digital motion processor (on MPU))
  Serial.println(F("Initializing DMP..."));
  devStatus = mpu.dmpInitialize();

  // set gyro offsets
  mpu.setXGyroOffset(220);
  mpu.setYGyroOffset(76);
  mpu.setZGyroOffset(-85);
  mpu.setZAccelOffset(1788);

  // make sure the MPU initialization worked (returns 0 if so)
  if (devStatus == 0) {

    // Generate offsets and calibrate MPU
    mpu.CalibrateAccel(6);
    mpu.CalibrateGyro(6);
    mpu.PrintActiveOffsets();

    // turn on the DMP
    Serial.println(F("Enabling DMP..."));
    mpu.setDMPEnabled(true);

    // enable Arduino interrupt detection
    Serial.print(F("Enabling interrupt detection (Arduino external interrupt "));
    Serial.print(digitalPinToInterrupt(INTERRUPT_PIN));
    Serial.println(F(")..."));
    attachInterrupt(digitalPinToInterrupt(INTERRUPT_PIN), dmpDataReady, RISING);
    mpuIntStatus = mpu.getIntStatus();

    // set DMP as "ready"
    Serial.println(F("DMP ready! Waiting for first interrupt..."));
    dmpReady = true;

    // get expected DMP packet size
    packetSize = mpu.dmpGetFIFOPacketSize();

  } else {
    // There is an error! See the output and debug.
    // 1 = initial memory load failed
    // 2 = DMP configuration updates failed
    Serial.print(F("DMP Initialization failed (code "));
    Serial.print(devStatus);
    Serial.println(F(")"));
  }
}

void loop() {

  // if MPU failed don't try to do anything
  if (!dmpReady) return;

  // read a packet from FIFO
  if (mpu.dmpGetCurrentFIFOPacket(fifoBuffer)) { // Get the Latest packet
    // display Euler angles in degrees from MPU
    mpu.dmpGetQuaternion(&q, fifoBuffer);
    mpu.dmpGetGravity(&gravity, &q);
    mpu.dmpGetYawPitchRoll(ypr, &q, &gravity);
    Serial.print("ypr\t");
    Serial.print(ypr[0] * 180 / M_PI);
    Serial.print("\t");
    Serial.print(ypr[1] * 180 / M_PI);
    Serial.print("\t");
    Serial.print(ypr[2] * 180 / M_PI);
    Serial.print("\t");
  }

  // Check whether there is data to be received
  if (radio.available()) {
    // Read the whole incoming data package and store it into the 'data' structure
    radio.read(&data, sizeof(Data_Package));
    lastReceiveTime = millis();
  }
  // Check whether we keep receving data, or we have lost connection between the two modules
  currentTime = millis();
  if ( currentTime - lastReceiveTime > 1000 ) { // If current time is >1 second since we have recived the last data, it has lost connection
    resetData(); // If connection is lost, reset the data. It prevents unwanted behavior.
  }
  
  // Print the joystick data that is recieved in the Serial Monitor
  //    Serial.print("; j1PotX: ");
  //    Serial.print(data.j1PotX);
  //    Serial.print("; j1PotY: ");
  //    Serial.print(data.j1PotY);
  //    Serial.print("; j2PotX: ");
  //    Serial.print(data.j2PotX);
  //    Serial.print("; j2PotY: ");
  //    Serial.print(data.j2PotY);
  //    Serial.print("; J1Button: ");
  //    Serial.print(data.j1Button);
  //    Serial.print("; J2Button: ");
  //    Serial.print(data.j2Button);
  //    Serial.println("");

  // Adjust motor speed based on joystick input.
  // Analog is between 0-255 (which is also what the is being inputted into it from the data structure)
  // Currently 1 axis controls the all motor speeds.

  // If negative roll, lower speed of pin 9 (Motor3)
  // If postive roll, lower speed of pin 3 (Motor1)
  // If negative pitch, lower speed of pin 5 (Motor2)
  // If positive pitch, lower speed of pin 10 (Motor4)

  // Adjusting motor speed based on tilt in order for quadcopter to balance - PID control

  // For motors 1 and 3
  error_R = target_angle + ypr[2];
  angleChange_R = kp * error_R; // Use adjustment factor (k)
  speedChange_R = map(angleChange_R, -180, 180, -255 , 255);
  if (speedChange_R < -1) {
    analogWrite(Motor3Pin, data.j1PotY + speedChange_R);
    analogWrite(Motor1Pin, data.j1PotY);
    motorSpeed3 = data.j1PotY + speedChange_R;
    motorSpeed1 = data.j1PotY;
  }
  else if (speedChange_R > 1) {
    analogWrite(Motor1Pin, data.j1PotY - speedChange_R);
    analogWrite(Motor3Pin, data.j1PotY);
    motorSpeed1 = data.j1PotY - speedChange_R;
    motorSpeed3 = data.j1PotY;
  }
  else {
    analogWrite(Motor1Pin, data.j1PotY);
    analogWrite(Motor3Pin, data.j1PotY);
    motorSpeed1 = data.j1PotY;
    motorSpeed3 = data.j1PotY;
  }

  // For motors 2 and 4
  error_P = target_angle + ypr[1];
  angleChange_P = kp * error_P;
  speedChange_P = map(angleChange_P, -180, 180, -255 , 255);
  if (speedChange_P < -1) {
    analogWrite(Motor2Pin, data.j1PotY + speedChange_P);
    analogWrite(Motor4Pin, data.j1PotY);
    motorSpeed2 = data.j1PotY + speedChange_P;
    motorSpeed4 = data.j1PotY;

  }
  else if (speedChange_P > 1) {
    analogWrite(Motor4Pin, data.j1PotY - speedChange_P);
    analogWrite(Motor2Pin, data.j1PotY);
    motorSpeed4 = data.j1PotY - speedChange_P;
    motorSpeed2 = data.j1PotY;
  }
  else {
    analogWrite(Motor2Pin, data.j1PotY);
    analogWrite(Motor4Pin, data.j1PotY);
    motorSpeed2 = data.j1PotY;
    motorSpeed4 = data.j1PotY;
  }

  // Print motor speeds
  Serial.print(motorSpeed1);
  Serial.print(", ");
  Serial.print(motorSpeed2);
  Serial.print(", ");
  Serial.print(motorSpeed3);
  Serial.print(", ");
  Serial.println(motorSpeed4);

}

// Reset the values when there is no radio connection
void resetData() {
  data.j1PotX = 0;
  data.j1PotY = 0;
  data.j2PotX = 0;
  data.j2PotY = 0;
  data.j1Button = 1;
  data.j2Button = 1;
}

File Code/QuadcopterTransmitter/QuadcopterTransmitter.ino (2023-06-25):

// Code for circuitboard that is placed on the Joystick (Arduino Uno) and is the "transmitter"

// Include libraries
#include <SPI.h>
#include <nRF24L01.h>
#include <RF24.h>
#include <Wire.h>

volatile int switchOnMotors = 0;
const byte interruptPin = 2;

// Define the joystick inputs
#define jB1 3  // Joystick button 1
#define jB2 4  // Joystick button 2
#define j1PotXPin A0 //Joystick 1 axis X
#define j1PotYPin A1 //Joystick 1 axis Y
#define j2PotXPin A2 //Joystick 2 axis X
#define j2PotYPin A3 //Joystick 2 axis Y

// ************ Initialize nRF24L01 variables *****************
RF24 radio(7, 8);   // nRF24L01 (CE, CSN)
const byte address[6] = "00010"; // Wireless communication address

// Max size of this struct is 32 bytes - NRF24L01 buffer limit
// Creating package to send data in (must match reciever package):
struct Data_Package {
  byte j1PotX;
  byte j1PotY;
  byte j1Button;
  byte j2PotX;
  byte j2PotY;
  byte j2Button;
};
Data_Package data; //Create a variable with the above structure

// Created button to remotely turn on and off the motors of the quadcopter
int buttonNew;
int buttonOld = 1;

void pushButton()
{
  buttonNew = digitalRead(interruptPin);
  if (buttonOld == 0 && buttonNew == 1) {
    if (switchOnMotors == 0) {
      switchOnMotors = 1;
    }
    else {
      switchOnMotors = 0;
    }
  }
  buttonOld = buttonNew;
}

void setup() {
  Serial.begin(9600); // Open serial port
  // Note: Baud rate at 115200 will make Serial fasterr but they will print out MPU slower than the joystick (in the transmitter)

  // Begin radio communication using nRF24L01
  radio.begin();
  radio.openWritingPipe(address);
  radio.setAutoAck(false);
  radio.setDataRate(RF24_250KBPS);
  radio.setPALevel(RF24_PA_MIN);

  // Activate the Arduino internal pull-up resistors
  pinMode(jB1, INPUT_PULLUP);
  pinMode(jB2, INPUT_PULLUP);

  // Set initial default values
  // Values are from 0 to 255. When Joystick is in resting position (middle), the value is 127.
  // The actual joystick gives 0 to 1023, but we map it to 0 to 255 in order to send one BYTE
  data.j1PotX = 0;
  data.j1PotY = 0;
  data.j2PotX = 0;
  data.j2PotY = 0;
  data.j1Button = 1;
  data.j2Button = 1;

  pinMode(interruptPin, INPUT_PULLUP);
  attachInterrupt(digitalPinToInterrupt(interruptPin), pushButton, CHANGE);
}

void loop() {
  // Check if button has been pressed once, if so then allow the values of the joystick to be sent to quadcopter, else send the value "0"
  if (switchOnMotors == 1) {
    // Read all analog inputs and map them to one Byte value
    // Convert the analog read value from 0 to 1023 into a BYTE value from 0 to 255
    data.j1PotX = map(analogRead(j1PotXPin), 0, 1023, 0, 255);
    data.j1PotY = map(analogRead(j1PotYPin), 0, 1023, 0, 255);
    data.j2PotX = map(analogRead(j2PotXPin), 0, 1023, 0, 255);
    data.j2PotY = map(analogRead(j2PotYPin), 0, 1023, 0, 255);
  }
  else {
    data.j1PotX = 0;
    data.j1PotY = 0;
    data.j2PotX = 0;
    data.j2PotY = 0;
  }

  // Read digital inputs
  data.j1Button = digitalRead(jB1);
  data.j2Button = digitalRead(jB2);

  // Send the data from the structure to the receiver
  radio.write(&data, sizeof(Data_Package));
}

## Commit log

2023-01-11 Uploaded Motor Dimensions
2023-01-19 Added models
    [GuardStand.SLDPRT, GuardStand.STL, GuardTest.ipt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]
2023-01-23 Added joystick to motor code
2023-01-27 Working on schematic
    [MiniCopterSchematic.kicad_pcb, MiniCopterSchematic.kicad_sch]
2023-01-27 Updating schematic
    [MiniCopterSchematic.kicad_sch]
2023-01-27 Finished Schematic
    [MiniCopterSchematic.kicad_sch]
2023-01-27 Updated schematic
    [MiniCopterSchematic.kicad_sch]
2023-01-28 Working on organizing perfboard
    [MiniCopterSchematic.kicad_sch]
2023-01-31 Combined MPU and nRF code
    [GuardV2.ipt, GuardV2.stl, MiniCopterSchematic.kicad_sch]
2023-02-14 Fixing files
    [PropellorGuardV2_Ashish.ipt, PropellorGuardV2_Ashish.stl]
2023-02-14 Working on chasssis
    [MiniCopterChassisV1.ipt, PropellorGuardV3.ipt]
2023-02-17 Working on 3D model for chassis
    [ChassisLeg.ipt, ChassisLegV1.ipt, MiniCopterChassis.ipt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]
2023-02-17 Working on assembly
    [MiniCopterAssembly.iam]
2023-02-17 Made major modifications to chassis to decrease weight
    [ChassisLeg.ipt, ChassisLegV1.ipt, GuardStand.SLDPRT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]
2023-02-22 Made prop guard thinner
    [PropellorGuardV6.ipt, PropellorGuardV6.stl]
2023-02-23 Organizing repo
    [ChassisLeg.ipt, ChassisLegV1.ipt, GuardStand.SLDPRT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]
2023-02-23 Updated schematic, added pictures, updated readme
    [MiniCopterSchematic.kicad_sch]
2023-02-27 Moved schematic to images folder
    [MiniCopterSchematic.kicad_pcb, MiniCopterSchematic.kicad_sch]
2023-03-01 Reduced weight of propeller gaurd
    [PropellorGuardLighter.ipt, PropellorGuardLighter.stl]
2023-03-08 Made chassis lighter
    [MiniCopterChassisLighterV2.ipt]
2023-03-30 Assigned footprints to symbols
    [MiniCopterSchematic.kicad_sch]
2023-04-03 Testing kp values for PID control
2023-04-06 Working on PCB for copter
    [MiniCopterSchematic.kicad_pcb, MiniCopterSchematic.kicad_sch]
2023-04-15 Working on PCB layout/wiring
    [MiniCopterSchematic.kicad_pcb, MiniCopterSchematic.kicad_sch]
2023-04-17 Working on PCB
    [MiniCopterSchematic.kicad_pcb, MiniCopterSchematic.kicad_sch]
2023-04-20 Fixing layout of components on PCB
    [MiniCopterSchematic.kicad_pcb]
2023-04-20 Working on PCB organizing and putting on text
    [MiniCopterSchematic.kicad_pcb, MiniCopterSchematic.kicad_sch]
2023-04-20 Fixed a lot of errors in the schematic which had caused PCB issues
    [MiniCopterSchematic.kicad_pcb, MiniCopterSchematic.kicad_sch]
2023-04-20 Working on PCB routing
    [MiniCopterSchematic.kicad_pcb, MiniCopterSchematic.kicad_sch]
2023-04-21 Organizing schematics
    [MiniCopterSchematic.kicad_pcb, MiniCopterSchematic.kicad_sch, MiniCopterTransmitterSchematic.kicad_pcb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]
2023-04-23 Working on routing
    [MiniCopterSchematic.kicad_pcb]
2023-04-25 Cleaning up board
    [MiniCopterSchematic.kicad_pcb]
2023-04-28 Added capacitor, changed track widths on PCB
    [MiniCopterSchematic.kicad_pcb, MiniCopterSchematic.kicad_sch]
2023-04-28 Added LEDs
    [MiniCopterSchematic.kicad_pcb, MiniCopterSchematic.kicad_sch]
2023-04-29 Making PCB look good
    [MiniCopterSchematic.kicad_pcb, MiniCopterSchematic.kicad_sch]
2023-04-29 Updated labels
    [MiniCopterSchematic.kicad_pcb, MiniCopterSchematic.kicad_sch]
2023-04-29 Added logos
    [MiniCopterSchematic.kicad_pcb]
2023-05-01 PCB design finalizing
    [MiniCopterSchematic.kicad_pcb, MiniCopterSchematic.kicad_sch]
2023-05-01 Finalizing PCB
    [MiniCopterSchematic.kicad_pcb]
2023-05-01 Fixed mosfet pinouts
    [MiniCopterSchematic.kicad_pcb]
2023-05-02 Finalized PCB
    [MiniCopterSchematic.kicad_pcb, MiniCopterSchematic.kicad_sch, MiniCopterTransmitterSchematic.kicad_sch]
2023-05-02 Created gerber files
    [MiniCopterSchematic-B_Cu.gbl, MiniCopterSchematic-B_Mask.gbs, MiniCopterSchematic-B_Paste.gbp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]
2023-05-02 Fixed size of pin holes
    [MiniCopterSchematic-B_Cu.gbl, MiniCopterSchematic-B_Mask.gbs, MiniCopterSchematic-B_Paste.gbp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]
2023-05-02 Created zip file for gerbers
2023-05-03 Updated PCB traces, added 5mm LEDS
    [MiniCopterSchematic.kicad_pcb, MiniCopterSchematic.kicad_sch]
2023-05-04 Made new gerber files
    [MiniCopterSchematic-B_Cu.gbl, MiniCopterSchematic-B_Mask.gbs, MiniCopterSchematic-B_Paste.gbp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]
2023-06-09 Updated models for pcb
    [MiniCopterChassis.ipt, MiniCopterChassisLessWeight.stl, MiniCopterChassisLighterV2.ipt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]
2023-06-22 Updated schematics and pics
    [MiniCopterSchematic.kicad_pcb, MiniCopterSchematic.kicad_sch, MiniCopterTransmitterSchematic.kicad_sch]
2023-06-25 Organized files
    [MiniCopterSchematic-B_Cu.gbl, MiniCopterSchematic-B_Mask.gbs, MiniCopterSchematic-B_Paste.gbp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]
